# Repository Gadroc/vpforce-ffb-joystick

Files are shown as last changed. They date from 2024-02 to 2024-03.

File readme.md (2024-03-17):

# VPForce Joystick
This is a remake of Mabo's FFB Joystick for 3D printing, with several enhancements from the protomaker's version as well.

Changes from Mambo's design:
* The gimbal is redesigned to minimize support material and optimize mating surfaces for fitment.
* 72 Tooth pulley used for 6:1 gear ratio
* Shell adjusted for 3D printing

Changes from Protomaker's design:
* Heat-set threaded inserts are used anywhere where a screw is used to fasten two printed parts.
* Single pot similar to Rhino
* No top panel cover
* Fan grate incorporated into case
* XT60 connector for power supply

# Credits
This design is nearly zero original work from me. All critical dimensions and ratios came from the original designers. I just cleaned up some CAD work and injected some of my preferences for 3D printing. Original authors are listed below:

* [walmis](https://github.com/walmis/FFB-Joystick-Base) - Electronics, firmware, and original base design.
* [mabo](https://github.com/mabo1972/FFB-Joystick-Base-Plywood) - Expanded base design, including full gimbal.
* [protomaker](https://github.com/protomaker964/Rhino-FFB-Clone-3D_Printed) - Modification for 3D printing and refinements

# Open Items
* I want to create a two-part stick adapter that uses metal tubing to allow people to select their own stick length. (Similar to the official VPRhino design by walmis)
* No throw limiters (I don't use one so didn't add it). Base has 22 degrees in all directions the same as the Rhino.
* Boot clamp has not been tested yet. Design changes may be necessary.
* CAD Still has a control board mount for under the gimbal, but there is not enough space to connect power wires in that location.
* Stick connector is designed for Thrustmaster replacement parts; I would like to create a version that will work for the [MD-50PL100](https://www.digikey.com/en/products/detail/cui-devices/MD-50PL100/500828). The stick connector from protomaker and mabo should be compatible, but I have not tested this.
* Optimize for screw types. There are a few places where we could eliminate screw variations (ex: bearing retainers vs case screws).
* Internal bearing retainer nuts are a pain, especially once motors are installed. Switch them to a captive nut.

# CAD
Both STEP and Fusion 360 files can be found in the CAD directory.

# Printed Parts
All STLs are in print orientation and should be able to be directly inserted and arranged in your slicer. I printed all my parts in polymaker PLA Pro with a .2mm layer height using voron part specs (4 walls and 45% grid infill). Adapt as necessary to your printer and filament.

| File | Qty | Support | Description |
|---|-----|---|---|
| gimbal_arm_x2 | 2 | Build Plate Only | Gimbal Arms |
| gimbal_pillow_x4 | 4 | Build Plate Only | Gimbal Pillow Blocks |
| gimbal_core | 1 | Build Plate Only | Gimbal Core Joint |
| gimbal_stick | 1 | Build Plate Only | Gimbal Stick Connector |
| ext_bearing_retainer_x3| 3 | None | Exterior Bearing Retainers |
| int_bearing_retainer_x8 | 8 | None | Interior Bearing Retainers |
| control_mount_retainer | 1 | None | Control Mount / Bearing retainer |
| case_rear | 1 | None | Rear Case Plate (Roll Drive) |
| case_right | 1 | None | Right Case Plate (Pitch Drive) |
| case_mid | 1 | None | Mid Case Plate (Roll Bearing / Control Mount) |
| case_front | 1 | None | Front Case Plate (Fan) |
| case_left | 1 | None | Left Case Plate (Pitch Bearing) |
| case_top | 1 | None | Case Top Plate |
| case_bottom | 1 | None | Bottom Case Plate |
| pulley_gimbal | 1 | 72 Tooth Gimbal Pulley |
| pulley_motor | None | 12 Tooth Motor Pulley (Optional if you don't want to buy metal pulley) |
| jig_center_x2 | 2 | Centering Jig for initial assembly and calibration |
| boot_clamp_lower | 1 | Lower Boot Clamp |
| boot_clamp_upper | 1 | Upper Boot Clamp |
| boot_clamp_ring | 1 | Boot Clamp Ring for Stick Connector |

# BOM
Where possible, all hardware has a McMaster Part # to help indicate correct specifications. When I didn't already have the parts in stock from old projects, I linked my actual source for them in the description.

| Qty | McMaster  | Name | Notes |
|-----|---|---|---|
| 4 | 4668K271  | [6808-2RS Bearings](https://www.amazon.com/dp/B0CGM2PG3Z) | Large Pulley Bearings |
| 8 | 5972k277  | [6802-2RS Bearings](https://www.amazon.com/dp/B0CGM2CHB8) | Gimbal Bearings |
| 2 | 57155k579 | [F625ZZ Bearings](https://www.amazon.com/dp/B07Z3DXF14) | Stick Adatper Bearings |
|  20 | 94459A150 | [M4 Threaded Inserts](https://www.amazon.com/dp/B08T9TXS9S) | Gimbal Screws |
|  10 | 92095A192 | [M4 x 12 Button Head Screw](https://www.amazon.com/dp/B09T9VFY5J) | Pulley Screws |
| 4 | 91100A313 | [19mm Washer](https://www.amazon.com/dp/B0B8SPK65J) | Gimbal Washers |
|  12 | 91292A122 | [M4 x 25 Socket Head Screw](https://www.amazon.com/dp/B0BMQ4WV1V) | Large Pulleys |
| 3 | 98689A114 | M5 Washer (Stock) | Gimbal Core Joint / Stick Adatper |
| 2 | 90591A260 | M5 Nut (Stock) | Gimbal Core Joint / Stick Adatper |
| 1 | 91290A199 | M5 x 60 Socket Head Screw (Stock) | Gimbal Core Joint |
|  52 | 94459A130 | [M3 Threaded Inserts](https://www.amazon.com/dp/B0CDH36ZMX) | Case, USB Bracket, Control Board Mount, Stick Connector |
|  44 | 91263A825 | [M3 x 12 Flat Head Screw](https://www.amazon.com/dp/B07WJKPCZY) | Case Screws, add two more if using printed motor pulleys |
| 2 | 92095A183 | M3 x 12 Button Head Screw (Stock) | USB Bracket Screws |
|  12 | 92095A119 | M3 x 15 Button Head Screw (Stock) | Pulley Bearing Retainer Screws |
|  12 | 90591A250 | M3 Nut (Stock) | Pulley Bearing Retainer Nuts |
| 4 | 92095A177 | M3 x 5 Button Head Screws (Stock) | Control Board Screws |
| 8 | | [M6 x 15 Slim Socket Head Screw](https://www.amazon.com/dp/B0CK264Y73) | Motor Mounts |
| 2 | | M2.5 x 10 Flat Head Screw (Stock) | Power Connector Mount |
| 2 | | M3 x 6 Grub Screw | Motor Pulley Screw for 3D Printed Pulley |
| 2 | | [5M-12T-16W Pulley](https://www.amazon.com/dp/B07R49G8BK) | Motor Pulley - 3D printed version is optional as well |
| 1 | | 465mm long HTD 5M-15W Belt | Pitch Belt |
| 1 | | 415mm long HTD 5M-15W Belt | Roll Belt |
| 1 | | 5 Pin Mini Din Connector (Stock)| Stick connector - I used replacement parts from Thrustmaster for a Warthog stick that I bought a long time ago. |
| 1 | | [80mm Case Fan](https://www.amazon.com/dp/B00IOIJ4AC) | Parts designed to use standard PC fan screws which are included with this fan. |
| 1 | | [E-Stop Switch](https://www.amazon.com/dp/B08B87GJGB) | |
| 1 | | [10k Type B Linear Potentiometer](https://www.amazon.com/dp/B09897HR3C) |
| 1 | | [XT60E-M Connector](https://www.amazon.com/dp/B07VV92WZS) | |

# Assembly
Since this is a very close derivative of protmakers work his assembly guide should be enough to figure out how to build using these parts.

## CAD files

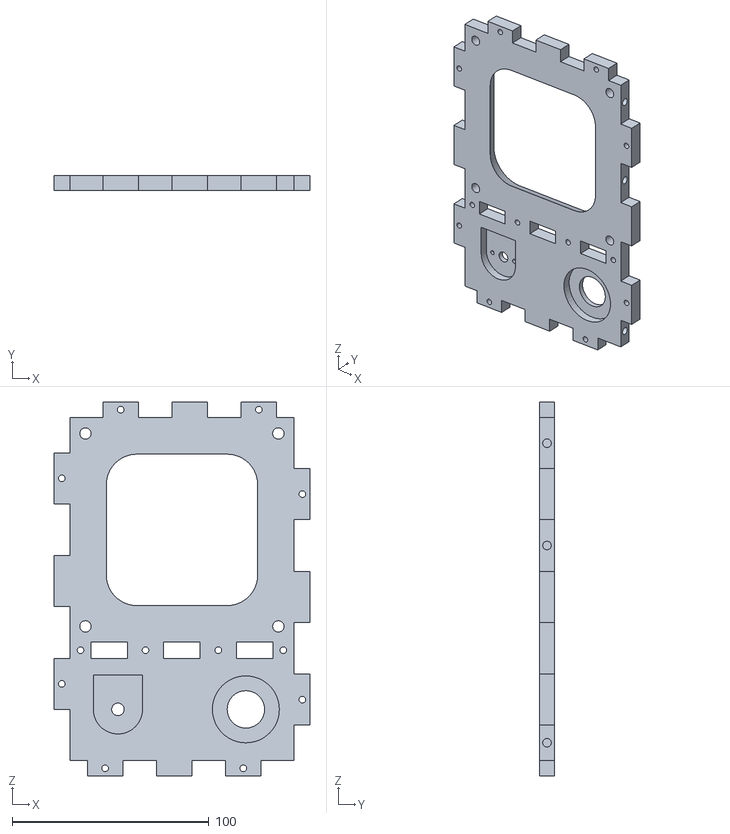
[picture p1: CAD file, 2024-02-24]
STL/case_top.stl
129.9 x 7.80 x 190.0

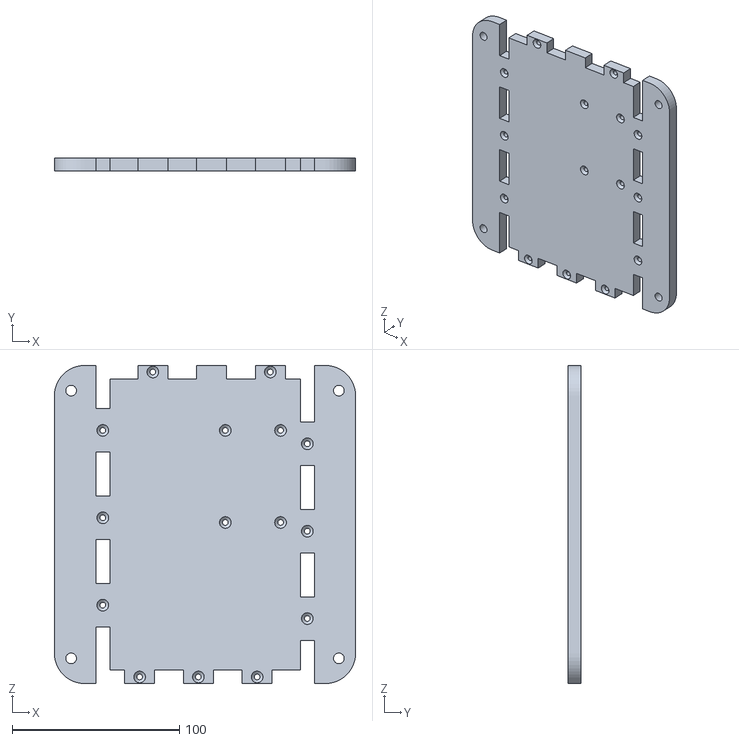
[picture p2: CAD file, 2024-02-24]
STL/case_bottom.stl
180.0 x 8.00 x 190.0

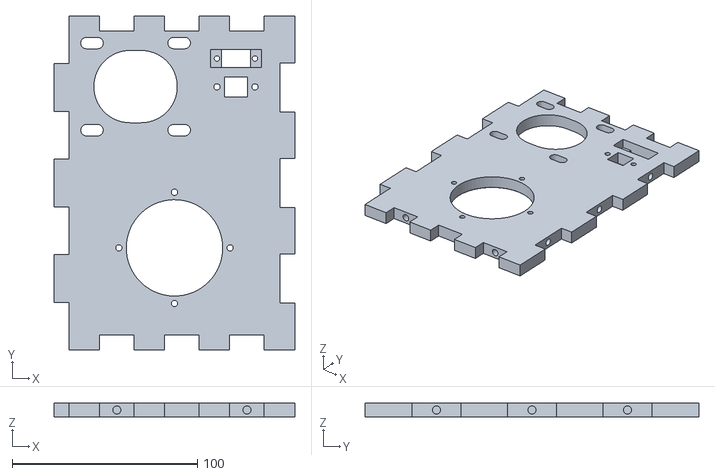
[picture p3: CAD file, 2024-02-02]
STL/case_rear.stl
130.0 x 180.0 x 7.80

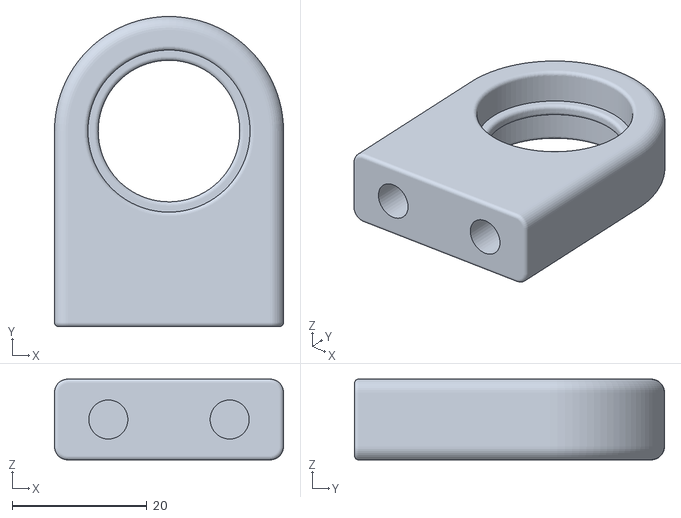
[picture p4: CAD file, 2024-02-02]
STL/gimbal_pillow_x4.stl
34.0 x 46.0 x 12.0

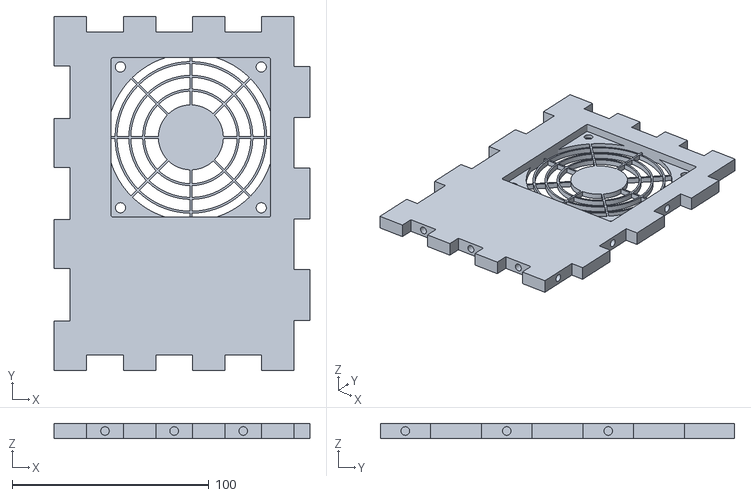
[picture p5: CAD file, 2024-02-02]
STL/case_front.stl
130.0 x 180.0 x 7.80

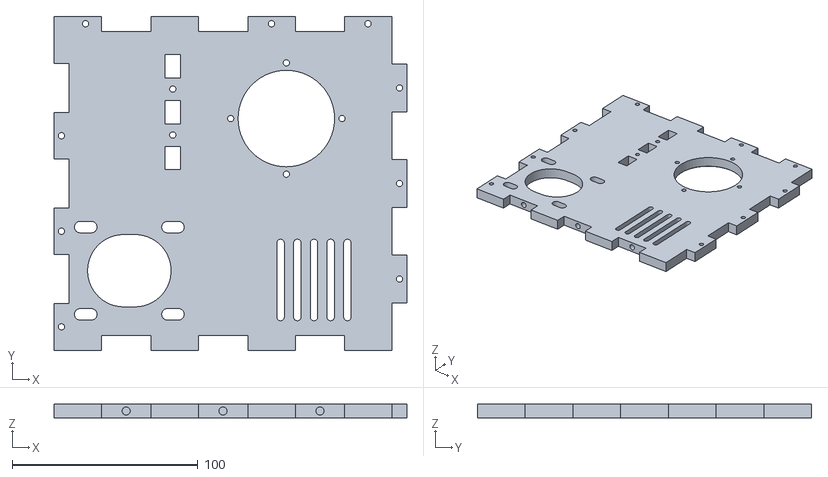
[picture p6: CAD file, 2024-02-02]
STL/case_right.stl
190.0 x 180.0 x 7.80

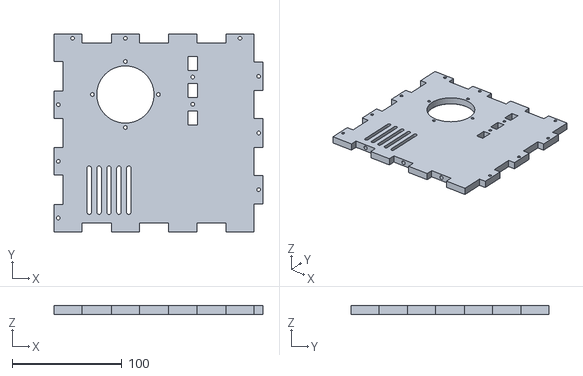
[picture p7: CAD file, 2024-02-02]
STL/case_left.stl
190.0 x 180.0 x 7.80

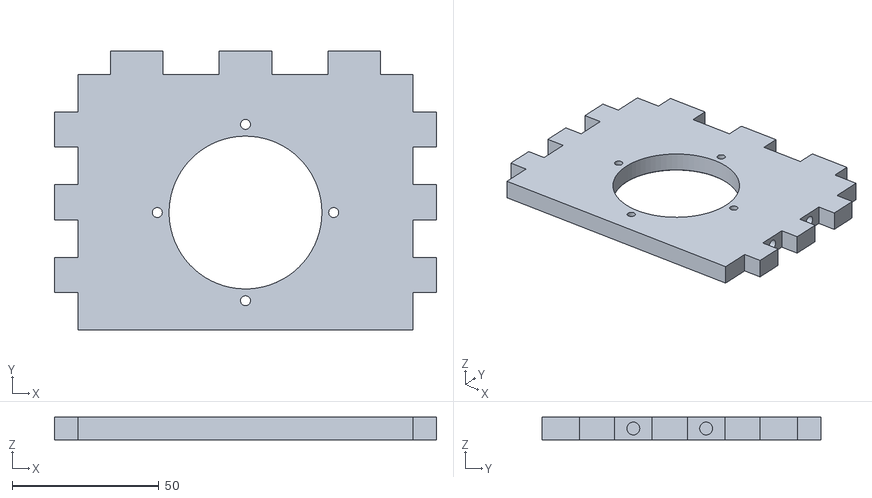
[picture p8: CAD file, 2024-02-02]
STL/case_mid.stl
130.0 x 95.0 x 7.80

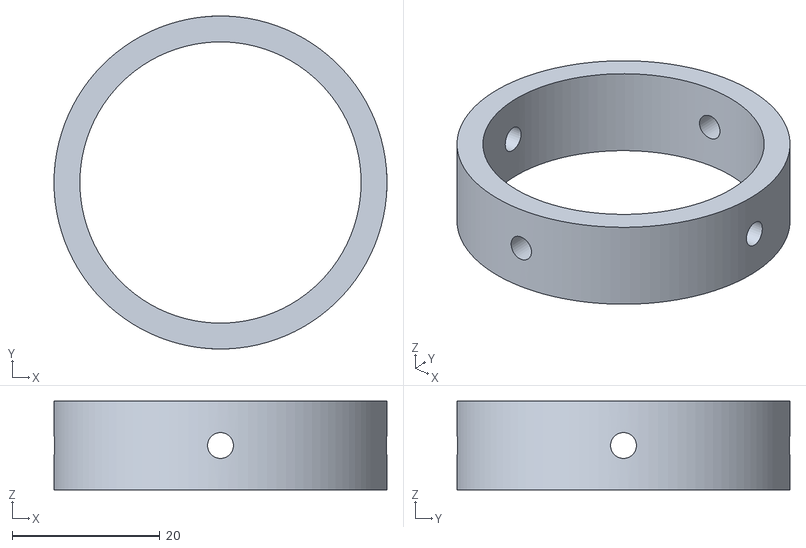
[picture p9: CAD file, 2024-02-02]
STL/boot_ring.stl
45.0 x 45.0 x 12.0

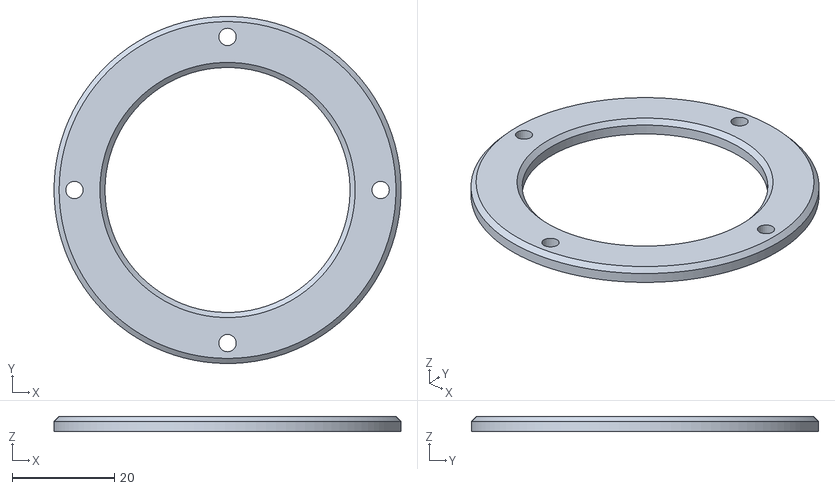
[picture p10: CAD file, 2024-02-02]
STL/ext_bearing_retainer_x3.stl
68.0 x 68.0 x 3.00

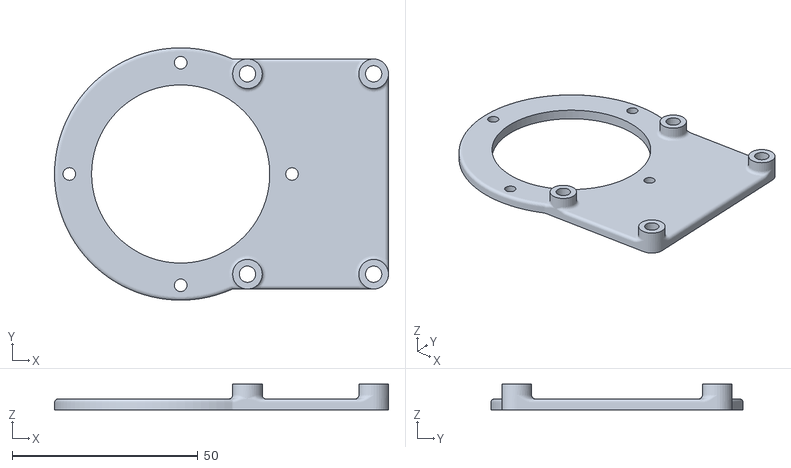
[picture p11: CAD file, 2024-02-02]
STL/control_mount_retainer.stl
90.0 x 68.0 x 7.00

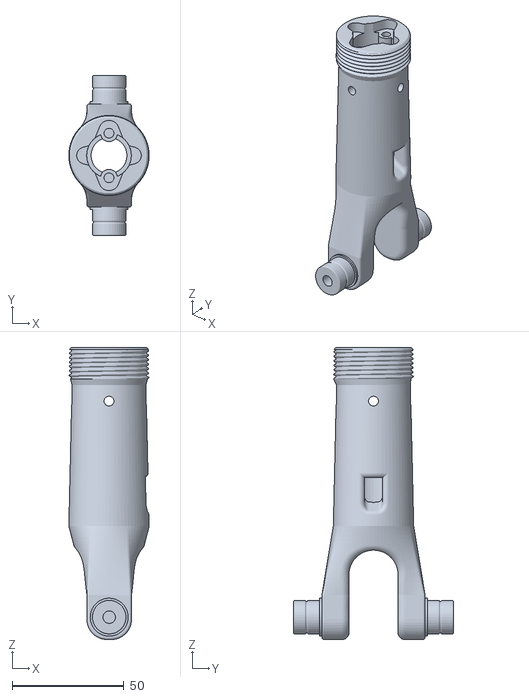
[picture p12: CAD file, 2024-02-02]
STL/gimbal_stick.stl
36.0 x 71.6 x 130.8

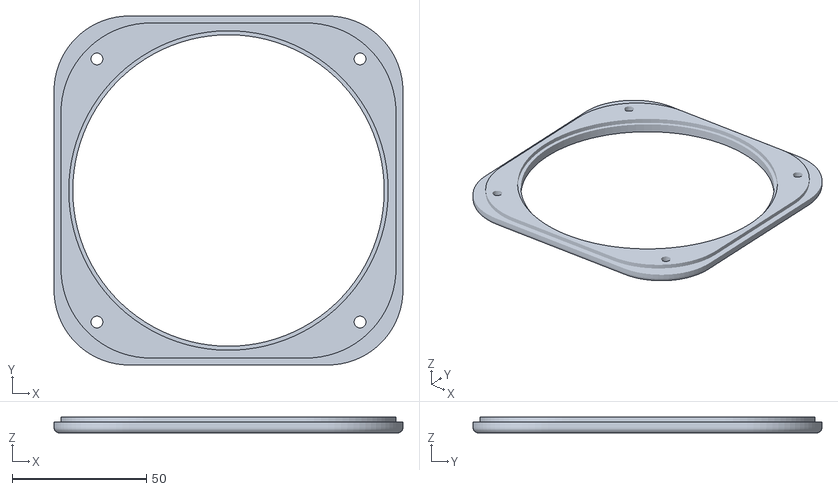
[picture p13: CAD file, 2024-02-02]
STL/boot_clamp_upper.stl
130.0 x 130.0 x 5.90

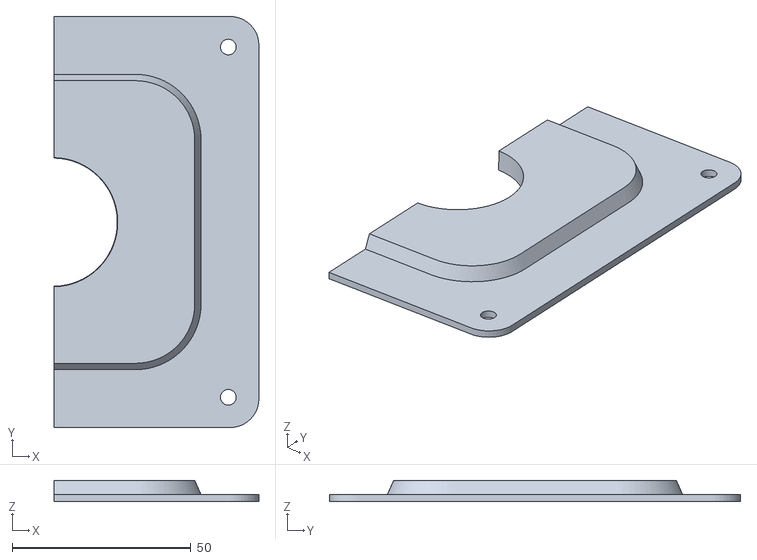
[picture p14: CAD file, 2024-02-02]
STL/center_jib_x2.stl
57.3 x 115.0 x 6.00

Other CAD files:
STL/pulley_motor.stl
STL/int_bearing_retainer_x8.stl
STL/gimbal_core.stl
STL/boot_clamp_lower.stl

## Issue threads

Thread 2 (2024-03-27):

3D Printing Optimisation

Michael-Jacobsen, 2024-03-27:
This is great. It is very much what I had planned to do to make some of the parts more print friendly. The heatset insert for the case are excellent, and the reduced overhangs in the gimble parts too.

Just a couple of suggestions;

Its good practice for the face that touches the build plate to use chamfers rather than fillets to minimise overhang and cooling issues, even if its only slight. Its generally easier to print a 45 degree slope rather than trying to 'role' the face up to vertical just to eliminate those few layers that have to form a steep overhang
Most refering to the gimble_arm part.
eg

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

VS

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

For any parts that may need to be printed with an overhanging counterbore its useful to use counterbore bridging features built into the model so the slicer does not try to print circles in mid air or to eliminate support use.
For example the gimble_stick part

eg

creating small bridges that step up one layer or 0.2mm in height at a time
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

She slicer shows the sequence for printing

The bore starts round
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

Four small bridges form the bore into a square profile
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

The next layer bridges into a hexagon bore
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

and finally the new narrow circular bore is easy to print without extra support
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

Gadroc, 2024-03-27:
Good calls.  I'll see about updating those when I get some time next week.

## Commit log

2024-02-24 Added missing STL files
    [case_bottom.stl, case_top.stl]
2024-03-17 Update readme.md
    Fix cut and paste typo on printed parts list
2024-03-17 Update readme.md
    Fix typo on belts
2024-03-17 Update readme.md
    Added HTD to belt description
